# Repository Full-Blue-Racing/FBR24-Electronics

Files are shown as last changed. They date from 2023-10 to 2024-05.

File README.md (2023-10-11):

# FBR24-Electronics

This repo houses all the code the car needs to run, separated into steering 
wheel, telemetry, and CAN bus files.

# Git Gud

[Git Crash Course](https://rogerdudler.github.io/git-guide/)

[Gitlab SSH setup](https://docs.gitlab.com/ee/ssh/)

Git can be separated into remote and local repository (repo), how it works is 
that you can *clone* a repo to your local machine, *add* files you would like 
git to track, *commit* your changes to your local branch, *pull* changes by 
others from the remote repo, and *push* your own local changes. Locally git can 
be separated into three areas:

```Untracked files -> tracked files -> staging area```

Untracked files are usually not part of the project and will not be added to the
repo. Tracked files are project files, and files in here will have status shown 
(i.e. new file/changed/renamed...). The staging area is files that are ready to 
be *committed*, and tracked files needs to be added by ```git add```.

These are the only commands I would recommend using on the command line/IDE, 
for more complex commands (such as creating pull requests for merging branches) 
use the web interface. 

![Image of Git Workflow](https://hackernoon.com/hn-images/1*mQdKYVN0nl-NvTw6MOSkWA.png)

# Best Practices

### No spaces in file names or folder names please

**No direct pushing/committing on the master branch**

1. Use branches

Each of the following tasks are on a separate 
branch, please work on the branch relevant to your task. If multiple people are 
on the same branch please make sub-branches from the main task branch 

*e.g.* 
```
steering-wheel -> steering-wheel-warninglights
               -> steering-wheel-RPM-lights
```

We will merge them into the main steering-wheel branch when you make a merge 
request to the task branch.

2. Micro-commit

Commit every time you've implemented a feature - it allows easy rollback to 
previous version without too much code loss if things go wrong (and they *WILL* 
go wrong).

3. Handy commands

```git config --global user.name <display name>``` - sets your name on your commits to the repo

```git clone <path/to/directory>``` - clones a local copy of the repo to your
machine so you can make changes.

```git pull origin <name of branch>``` - pulls any changes others have 
published on the remote branch of the said name since your last update/ initial 
clone

```git add <file to be added>``` - adds file to the staging area to be included 
in the next commit.

```git commit -m "Commit message here"``` - commits file to the local branch 
with the commit message - please make the commit message meaningful so it is 
easier to backtrack (**Not** ```Add new file```) 

```git push origin <name of branch>``` - push your local commits to the remote 
repo on the named branch. Note that on the first push git may require you to 
set the upstream branch with ```git branch --set-upstream-to <name of head branch>```

```git remote update origin --prune``` - updates branches and removes merged branches 
on your local machine.

# Tasks

Each function to be made are described in respective folders' ```README```,
please edit the ```README``` with your name if you are currently working on the 
task, and remove it if not. If someone is already working on one and you want 
to join, contact them and see if you can help before writing your own code. 
Otherwise just write your name down and contact me (Will) for any 
questions/purchasing.

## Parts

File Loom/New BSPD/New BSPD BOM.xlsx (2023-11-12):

Component Count: | 46
Collated Components:
Item | Qty | Reference(s) | Value | LibPart | Footprint | Datasheet | DNP | Sim.Device | Sim.Pins
1 | 1 | C1 | C | Device:C |  | ~
2 | 1 | D1 | 1N5817 | Diode:1N4001 | Diode_THT:D_DO-41_SOD81_P10.16mm_Horizontal | http://www.vishay.com/docs/88503/1n4001.pdf |  | D | 1=K 2=A
3 | 4 | D2, D3, D4, D5 | LED | Device:LED | LED_THT:LED_D5.0mm | ~
4 | 2 | J1, J2 | 282087-1 | Connector:Conn_01x03_Female | Additional Footprints:3 pin flying lead | https://www.te.com/usa-en/product-282087-1.html
5 | 1 | J3 | 282105-1 | Connector:Conn_01x03_Female | Additional Footprints:3 pin flying lead | https://www.te.com/usa-en/product-282105-1.datasheet.pdf
6 | 1 | J4 | Screw_Terminal_01x02 | Connector:Screw_Terminal_01x02 |  | ~
7 | 4 | JP1, JP2, JP3, JP4 | SolderJumper_3_Open | Jumper:SolderJumper_3_Open | Jumper:SolderJumper-3_P1.3mm_Open_RoundedPad1.0x1.5mm | ~
8 | 1 | K1 | MCCMA51-S-DC12V-C | Additional_Components:Relay | Additional Footprints:MCCMA51-S-DC12V-C | https://www.farnell.com/datasheets/3169904.pdf
9 | 1 | Q1 | IRLZ44Z | Transistor_FET:IRLZ44N | Package_TO_SOT_THT:TO-220-3_Vertical | http://www.irf.com/product-info/datasheets/data/irlz44n.pdf
10 | 2 | R1, R2 | 5Meg | Device:R | Resistor_THT:R_Axial_DIN0207_L6.3mm_D2.5mm_P7.62mm_Horizontal | ~
11 | 1 | R3 | 4.7k | Device:R | Resistor_THT:R_Axial_DIN0207_L6.3mm_D2.5mm_P7.62mm_Horizontal | ~
12 | 4 | R4, R5, R6, R7 | 220R | Device:R | Resistor_THT:R_Axial_DIN0207_L6.3mm_D2.5mm_P7.62mm_Horizontal | ~
13 | 1 | R8 | R | Device:R |  | ~
14 | 4 | RV1, RV2, RV3, RV4 | 10k | Device:R_Potentiometer | Potentiometer_THT:Potentiometer_Bourns_3296Y_Vertical | ~
15 | 1 | RV5 | R_Potentiometer | Device:R_Potentiometer |  | ~
16 | 8 | U1, U2, U3, U4, U5, U6, U7, U8 | 4011 | 4xxx:4011 | Package_DIP:DIP-14_W7.62mm_Socket | http://www.intersil.com/content/dam/Intersil/documents/cd40/cd4011bms-12bms-23bms.pdf
17 | 2 | U9, U10 | LM2901 | Comparator:LM2901 |  | https://www.st.com/resource/en/datasheet/lm2901.pdf
18 | 1 | U11 | 4012 | 4xxx:4012 | Package_DIP:DIP-14_W7.62mm_Socket | http://www.intersil.com/content/dam/Intersil/documents/cd40/cd4011bms-12bms-23bms.pdf
19 | 1 | U12 | 74LS573 | 74xx:74LS573 |  | 74xx/74hc573.pdf
20 | 3 | U13, U14, U15 | 4040 | 4xxx:4040 |  | http://www.intersil.com/content/dam/Intersil/documents/cd40/cd4020bms-24bms-40bms.pdf
21 | 1 | U16 | L7805 | Regulator_Linear:L7805 |  | http://www.st.com/content/ccc/resource/technical/document/datasheet/41/4f/b3/b0/12/d4/47/88/CD00000444.pdf/files/CD00000444.pdf/jcr:content/translations/en.CD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
22 | 1 | X1 | ASZKDV-32.768KHz | BSPD Symbols:ASZKDV-xxxMHz | Oscillator:Oscillator_SMD_Abracon_ASE-4Pin_3.2x2.5mm | http://www.abracon.com/Oscillators/ASV.pdf

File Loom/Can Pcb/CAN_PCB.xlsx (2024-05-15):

# | Reference | Qty | Value | Footprint | DNP
1 | C1, C2 | 2 | 27pF | Capacitor_THT:C_Disc_D4.7mm_W2.5mm_P5.00mm
2 | D1 | 1 | PWR LED | LED_THT:LED_D3.0mm
3 | J2 | 1 | Conn_01x05_Pin | Connector_PinHeader_2.54mm:PinHeader_1x05_P2.54mm_Vertical
4 | J3 | 1 | Screw_Terminal_01x02 | TerminalBlock:TerminalBlock_bornier-2_P5.08mm
5 | J4 | 1 | Conn_01x02 | Footprints:ATF13-2P-BM03
6 | J5, J12, J15, J16 | 4 | Conn_01x03 | BSPD_footprints:ATF13-3P-BM03
7 | JP1, JP4, JP5, JP8 | 4 | SolderJumper_3_Open | Jumper:SolderJumper-3_P1.3mm_Open_Pad1.0x1.5mm | No Fit
8 | R1 | 1 | 20K | Resistor_THT:R_Axial_DIN0207_L6.3mm_D2.5mm_P7.62mm_Horizontal
9 | R2 | 1 | 220R | Resistor_THT:R_Axial_DIN0207_L6.3mm_D2.5mm_P7.62mm_Horizontal
10 | R3, R6, R7, R10 | 4 | 5Meg | Resistor_THT:R_Axial_DIN0207_L6.3mm_D2.5mm_P7.62mm_Horizontal
11 | U1 | 1 | MCP25050-I/P | Package_DIP:DIP-14_W7.62mm_Socket | Sockets and chip
12 | U2 | 1 | MCP2551-I-P | Package_DIP:DIP-8_W7.62mm_Socket | Sockets and chip
13 | U4 | 1 | TL780-05KCS | Package_TO_SOT_THT:TO-220-3_Horizontal_TabDown
14 | Y1 | 1 | Crystal | Footprints:9B-16.000MAAJ-B

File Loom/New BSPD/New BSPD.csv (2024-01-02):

Id | Designator | Footprint | Quantity | Designation | Supplier and ref
1 | D7,D4,D2,D8,D6,D3,D5 | LED_D5.0mm | 7 | LED
2 | R10,R11,R7,R9,R6,R5,R4 | R_Axial_DIN0207_L6.3mm_D2.5mm_P7.62mm_Horizontal | 7 | 220R
3 | JP1,JP2,JP4,JP3 | SolderJumper-3_P1.3mm_Open_RoundedPad1.0x1.5mm | 4 | SolderJumper_3_Open
4 | U12 | DIP-20_W7.62mm_Socket | 1 | 74LS573
5 | U3,U5,U2,U6,U8,U1,U7,U4 | DIP-14_W7.62mm_Socket | 8 | 4011
6 | RV2,RV3,RV1,RV4 | Potentiometer_Bourns_3296Y_Vertical | 4 | 10k
7 | C1 | C_Disc_D5.0mm_W2.5mm_P5.00mm | 1 | 100n
8 | U11 | DIP-14_W7.62mm_Socket | 1 | 4012
9 | U14,U13,U15 | DIP-16_W7.62mm_Socket | 3 | 4040
10 | K1 | MCCMA51-S-DC12V-C | 1 | MCCMA51-S-DC12V-C
11 | R3 | R_Axial_DIN0207_L6.3mm_D2.5mm_P7.62mm_Horizontal | 1 | 4.7k
12 | R8 | R_Axial_DIN0207_L6.3mm_D2.5mm_P7.62mm_Horizontal | 1 | 1M
13 | TP4,TP3,TP2,TP1 | TestPoint_THTPad_D3.0mm_Drill1.5mm | 4 | TestPoint
14 | J3,J2,J1 | ATF13-3P-BM03 | 3 | Conn_01x03
15 | Q1 | TO-220-3_Horizontal_TabDown | 1 | IRLZ44Z
16 | U9,U10 | DIP-14_W7.62mm_Socket | 2 | LM2901
17 | C2 | C_0603_1608Metric_Pad1.08x0.95mm_HandSolder | 1 | 10u
18 | U16 | TO-220-3_Horizontal_TabDown | 1 | L7805
19 | X1 | Oscillator_SMD_Abracon_ASE-4Pin_3.2x2.5mm | 1 | ASZKDV-32.768KHz
20 | D1 | D_DO-41_SOD81_P10.16mm_Horizontal | 1 | 1N5817
21 | R1,R2 | R_Axial_DIN0207_L6.3mm_D2.5mm_P7.62mm_Horizontal | 2 | 5Meg
22 | J4 | TerminalBlock_bornier-2_P5.08mm | 1 | Screw_Terminal_01x02
23 | RV5 | Potentiometer_Bourns_3296Y_Vertical | 1 | R_Potentiometer

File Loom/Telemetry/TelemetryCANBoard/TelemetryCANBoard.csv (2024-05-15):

Source: | /home/charlotte/Documents/FBR/FBR24-Electronics/Loom/Telemetry/TelemetryCANBoard/TelemetryCANBoard.kicad_sch
Date: | Sun 12 Nov 2023 15:14:25 GMT
Tool: | Eeschema 7.0.8
Generator: | /usr/share/kicad/plugins/bom_csv_grouped_by_value.py
Component Count: | 11
Collated Components:
Item | Qty | Reference(s) | Value | LibPart | Footprint | Datasheet | DNP
1 | 2 | C1, C2 | 27p | Device:C_Small |  | ~
2 | 2 | J1, J2 | Conn_01x06 | Connector_Generic:Conn_01x06 |  | ~
3 | 1 | J3 | Conn_01x02 | Connector_Generic:Conn_01x02 |  | ~
4 | 1 | R1 | 20k | Device:R |  | ~
5 | 1 | R2 | 10k | Device:R |  | ~
6 | 1 | R3 | 120 | Device:R |  | ~
7 | 1 | U1 | MCP2551-I-P | Interface_CAN_LIN:MCP2551-I-P | Package_DIP:DIP-8_W7.62mm | http://ww1.microchip.com/downloads/en/devicedoc/21667d.pdf
8 | 1 | U2 | MCP2515-xSO | Interface_CAN_LIN:MCP2515-xSO | Package_SO:SOIC-18W_7.5x11.6mm_P1.27mm | http://ww1.microchip.com/downloads/en/DeviceDoc/21801e.pdf
9 | 1 | Y1 | 16M | Device:Crystal |  | ~

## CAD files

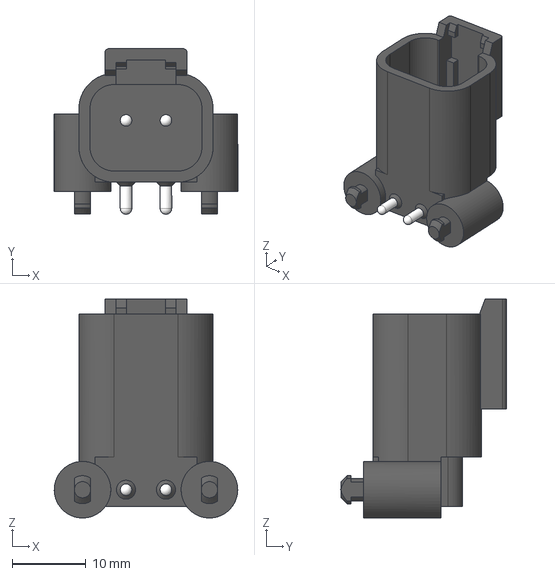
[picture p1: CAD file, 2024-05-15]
Loom/Can Pcb/Footprints/AMPHENOLSINE_ATF132PBM03/ATF13-2P-BM03.stp
24.8 x 22.4 x 29.6 mm

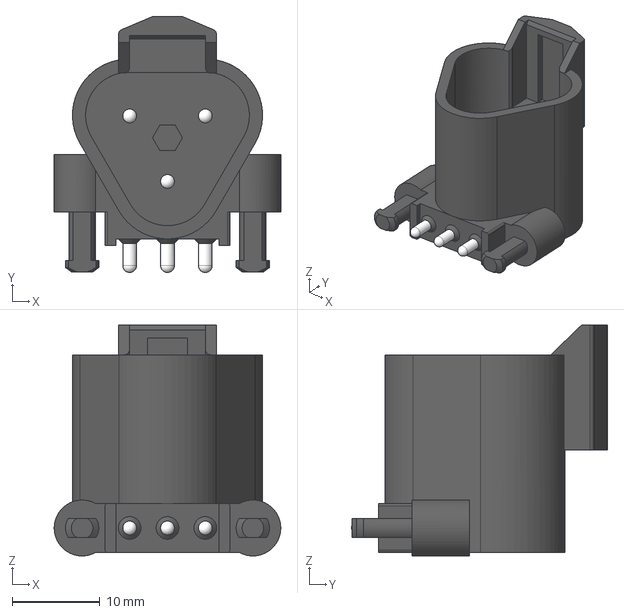
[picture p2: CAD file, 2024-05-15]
Loom/Can Pcb/Footprints/AMPHENOLSINE_ATF133PBM03 2/ATF13-3P-BM03.stp
25.8 x 29.1 x 26.3 mm

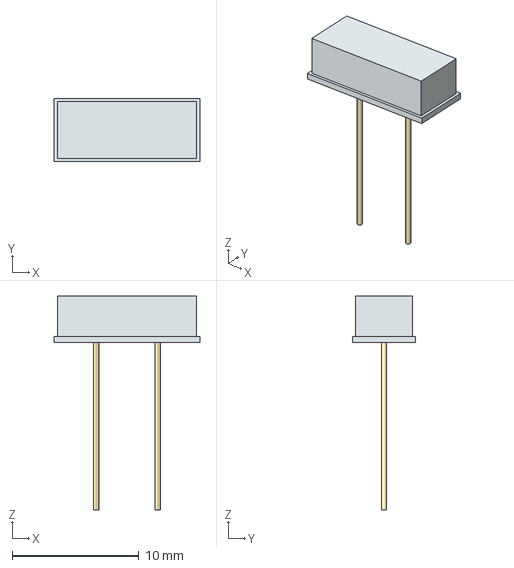
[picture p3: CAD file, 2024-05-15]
Loom/Can Pcb/Footprints/LIB_9B-16.000MAAJ-B/9B-16.000MAAJ-B/3D/9B-16.000MAAJ-B.stp
11.5 x 5.00 x 16.9 mm
solidBody
solidLead

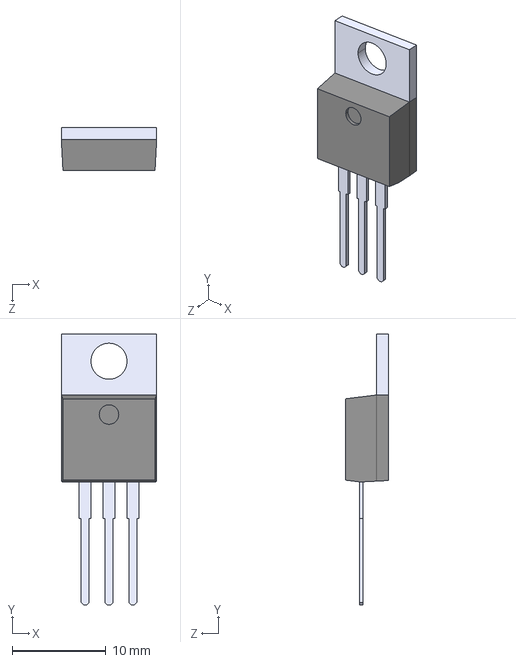
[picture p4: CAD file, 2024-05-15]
Loom/Can Pcb/Footprints/TO254P1036X470X1965-3.step
10.2 x 28.9 x 4.55 mm

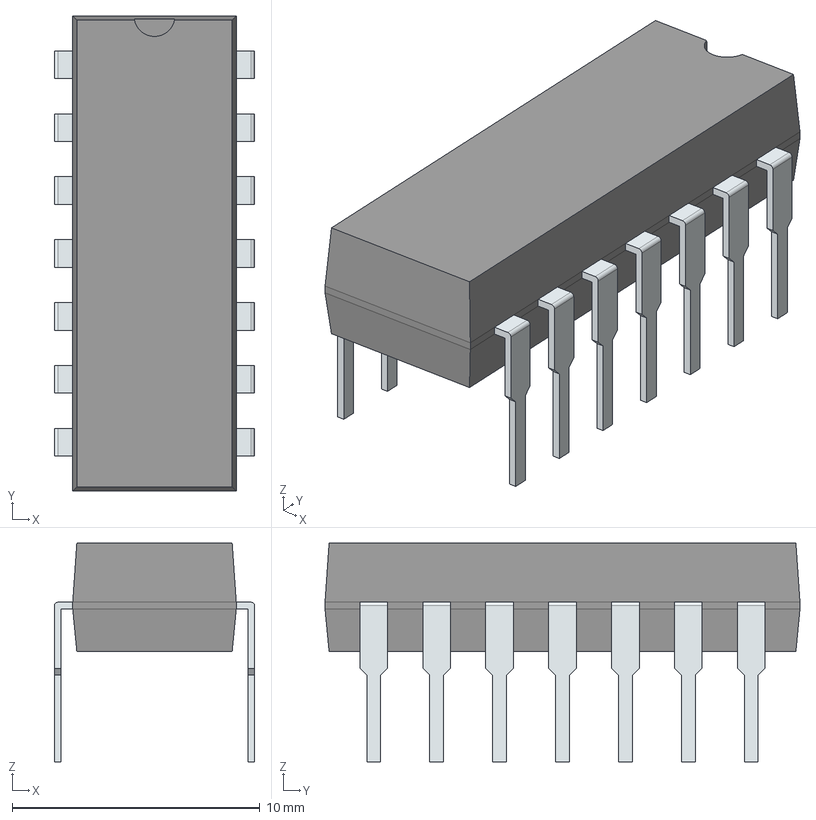
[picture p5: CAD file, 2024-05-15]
Loom/Can Pcb/Footprints/mcp6004-e_p.stp
8.09 x 19.2 x 8.83 mm
PinsArrayLR

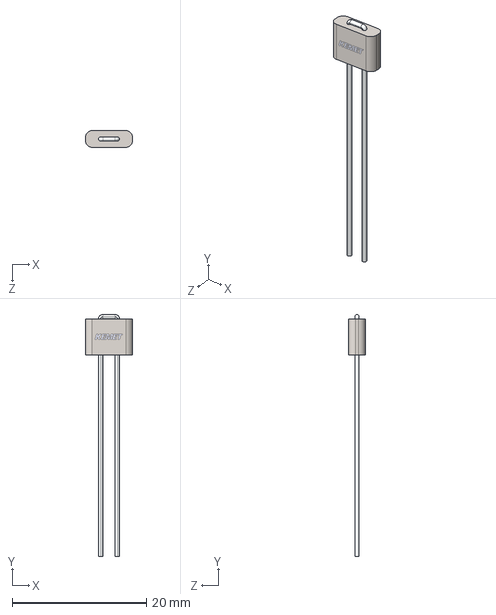
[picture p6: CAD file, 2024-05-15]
Loom/Can Pcb/Footprints/B-06-R-25.step
7.00 x 36.0 x 2.50 mm

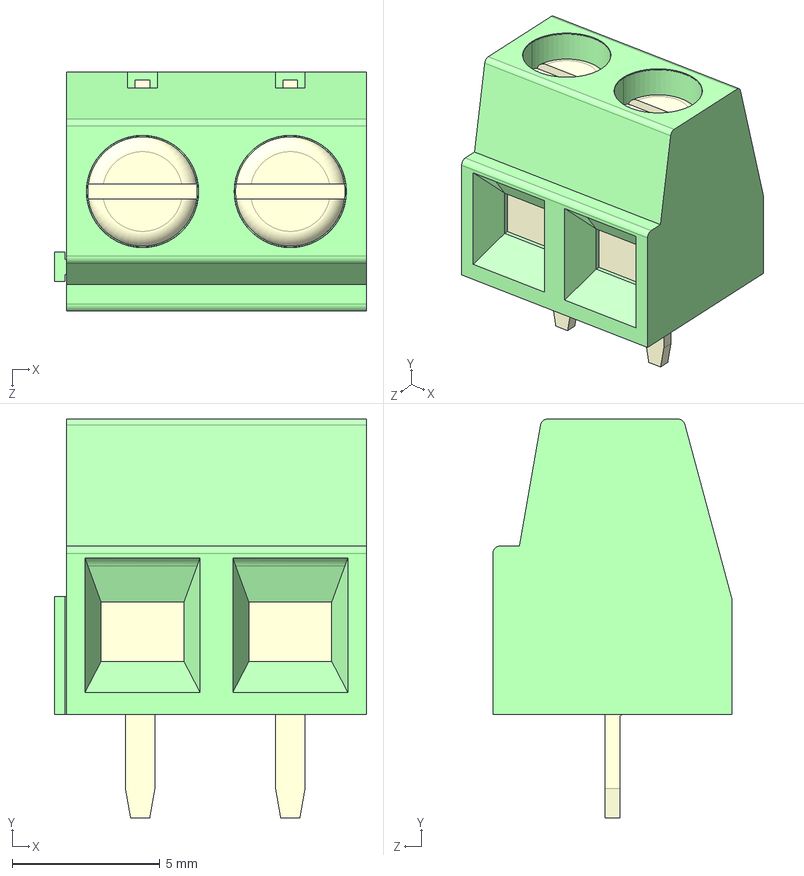
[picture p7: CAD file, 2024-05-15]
Loom/Can Pcb/Footprints/LIB_1729128/1729128/3D/1729128.stp
10.6 x 13.5 x 8.10 mm

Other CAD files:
Loom/Can Pcb/Footprints/AMPHENOLSINE_ATF133PBM03/ATF13-3P-BM03.stl
Loom/Can Pcb/Footprints/LIB_1729128/1729128/Allegro/1729128.psm
Loom/Can Pcb/Footprints/LIB_1729128/1729128/DEHDL/1729128/chips/chips.prt
Loom/Can Pcb/Footprints/LIB_9B-16.000MAAJ-B/9B-16.000MAAJ-B/Allegro/9b16000maajb.psm
Loom/Can Pcb/Footprints/LIB_9B-16.000MAAJ-B/9B-16.000MAAJ-B/DEHDL/9b_16.000maaj_b/chips/chips.prt

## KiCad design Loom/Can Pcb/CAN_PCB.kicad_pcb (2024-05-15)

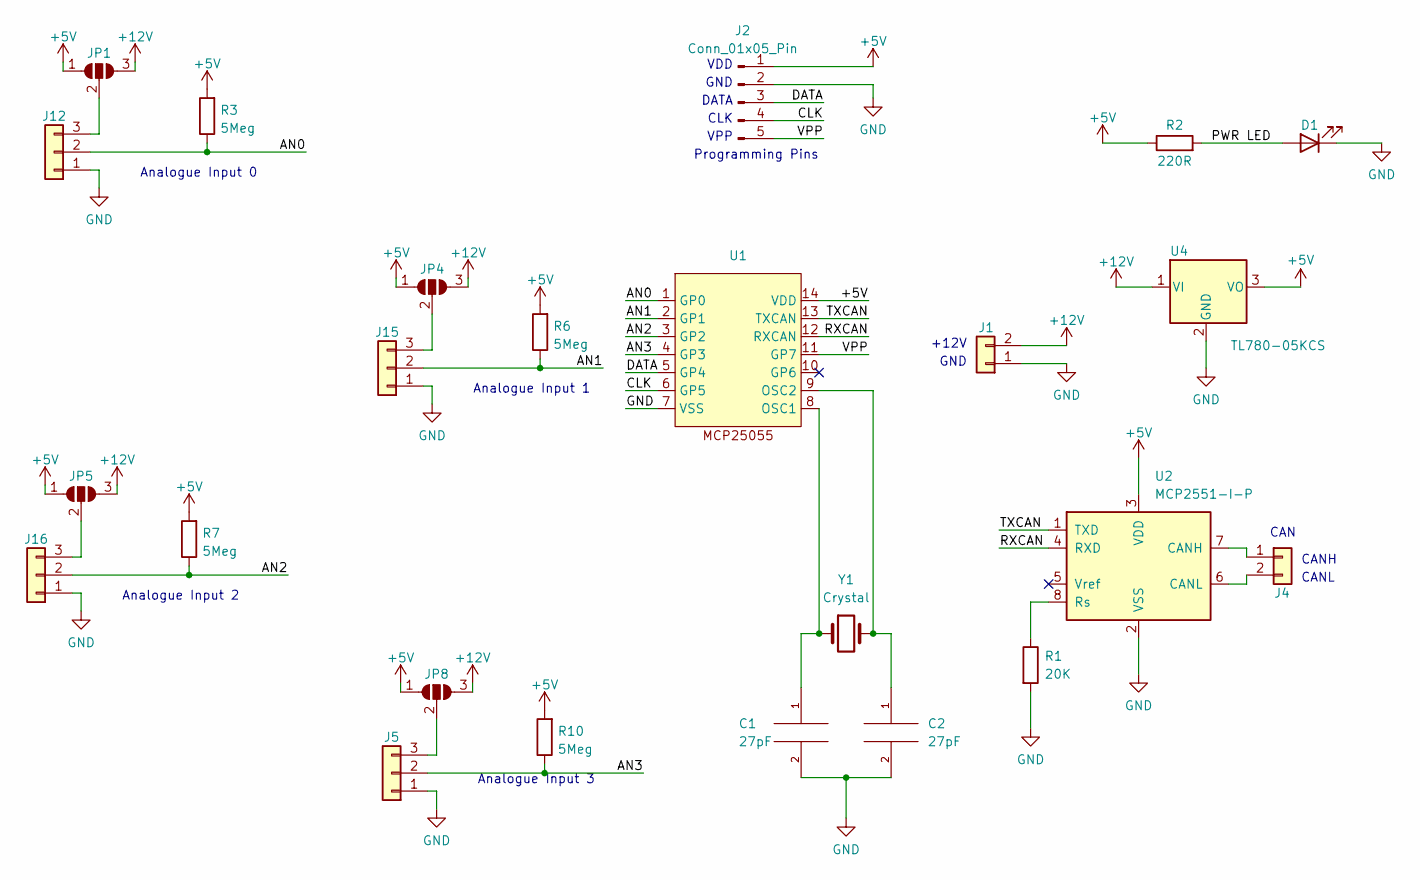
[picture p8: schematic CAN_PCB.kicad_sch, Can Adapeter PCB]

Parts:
C1, C2: 27pF; C_Disc_D4.7mm_W2.5mm_P5.00mm
D1: PWR LED; LED_D3.0mm
J1, J4: Conn_01x02; ATF13-2P-BM03
J2: Conn_01x05_Pin; PinHeader_1x05_P2.54mm_Vertical
J5, J12, J15, J16: Conn_01x03; ATF13-3P-BM03
JP1, JP4, JP5, JP8: SolderJumper_3_Open; SolderJumper-3_P1.3mm_Open_Pad1.0x1.5mm
R1: 20K; R_Axial_DIN0207_L6.3mm_D2.5mm_P7.62mm_Horizontal
R2: 220R; R_Axial_DIN0207_L6.3mm_D2.5mm_P7.62mm_Horizontal
R3, R6, R7, R10: 5Meg; R_Axial_DIN0207_L6.3mm_D2.5mm_P7.62mm_Horizontal
U1: DIP-14_W7.62mm_Socket
U2: MCP2551-I-P; DIP-8_W7.62mm_Socket
U4: TL780-05KCS; TO-220-3_Horizontal_TabDown
Y1: Crystal; 9B-16.000MAAJ-B

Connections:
+5V: J2.1, JP1.1 (A), JP4.1 (A), JP5.1 (A), JP8.1 (A), R2.1, R3.2, R6.2, R7.2, R10.2, U1.14 (VDD), U2.3 (VDD), U4.3 (VO)
+12V: J1.2, JP1.3 (B), JP4.3 (B), JP5.3 (B), JP8.3 (B), U4.1 (VI)
/AN0: J12.2, R3.1, U1.1 (GP0)
/AN1: J15.2, R6.1, U1.2 (GP1)
/AN2: J16.2, R7.1, U1.3 (GP2)
/AN3: J5.2, R10.1, U1.4 (GP3)
/CLK: J2.4, U1.6 (GP5)
/DATA: J2.3, U1.5 (GP4)
/PWR LED: D1.2 (A), R2.2
/RXCAN: U1.12 (RXCAN), U2.4 (RXD)
/TXCAN: U1.13 (TXCAN), U2.1 (TXD)
/VPP: J2.5, U1.11 (GP7)
GND: C1.2, C2.2, D1.1 (K), J1.1, J2.2, J5.1, J12.1, J15.1, J16.1, R1.2, U1.7 (VSS), U2.2 (VSS), U4.2 (GND)
unnamed: J4.1, U2.7 (CANH)
unnamed: J4.2, U2.6 (CANL)
unnamed: J5.3, JP8.2 (C)
unnamed: J12.3, JP1.2 (C)
unnamed: J15.3, JP4.2 (C)
unnamed: J16.3, JP5.2 (C)
unnamed: C1.1, U1.8 (OSC1), Y1.1
unnamed: C2.1, U1.9 (OSC2), Y1.2
unnamed: R1.1, U2.8 (Rs)

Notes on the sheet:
CAN
DATA
+12V
Analogue Input 2
VDD
Programming Pins
CANL
Analogue Input 3
Analogue Input 0
VPP
GND
CANH
CLK
Analogue Input 1

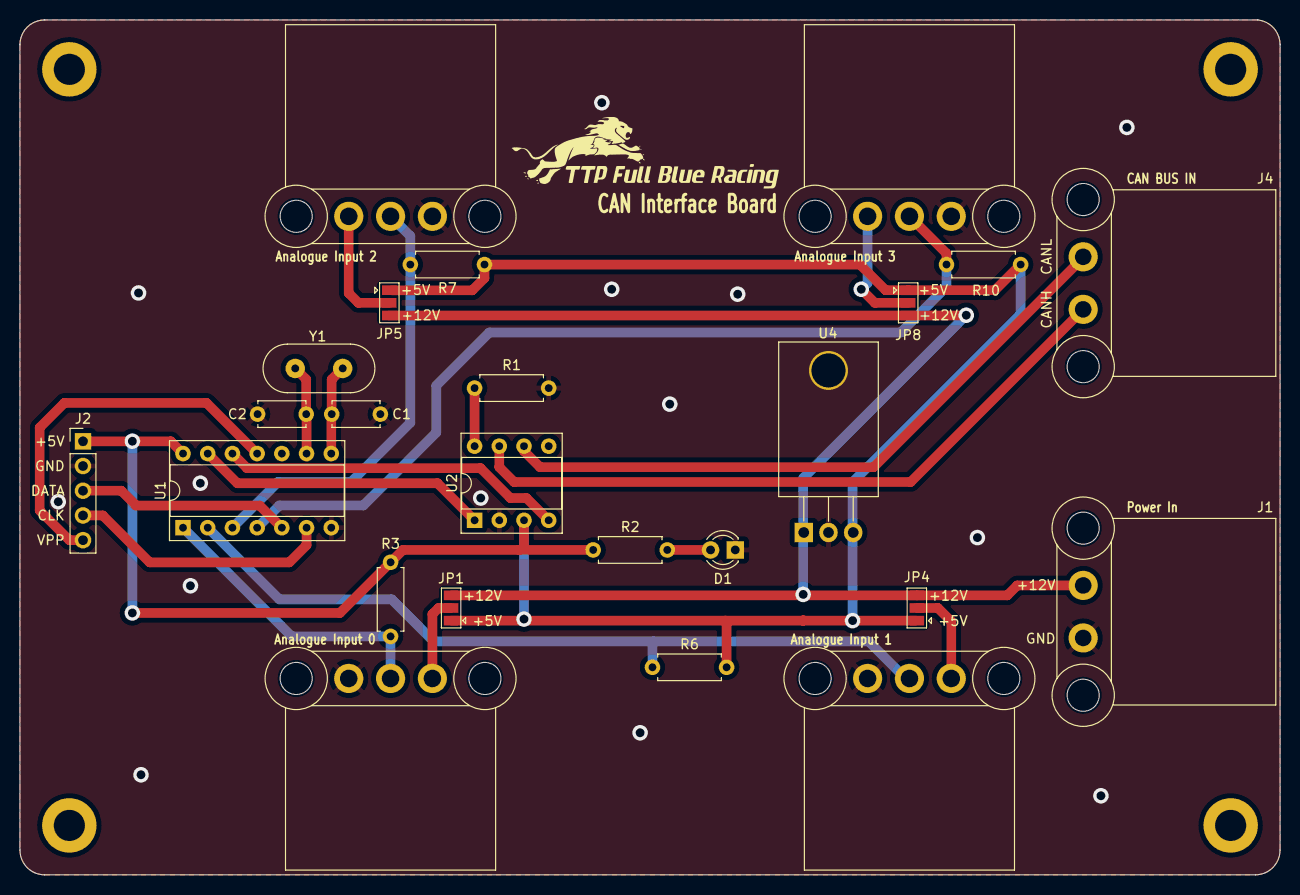
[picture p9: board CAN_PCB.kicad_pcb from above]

Board: 2 copper layers, 129.5 x 87.9 mm, 24 parts (0 on the bottom side), 22 nets.

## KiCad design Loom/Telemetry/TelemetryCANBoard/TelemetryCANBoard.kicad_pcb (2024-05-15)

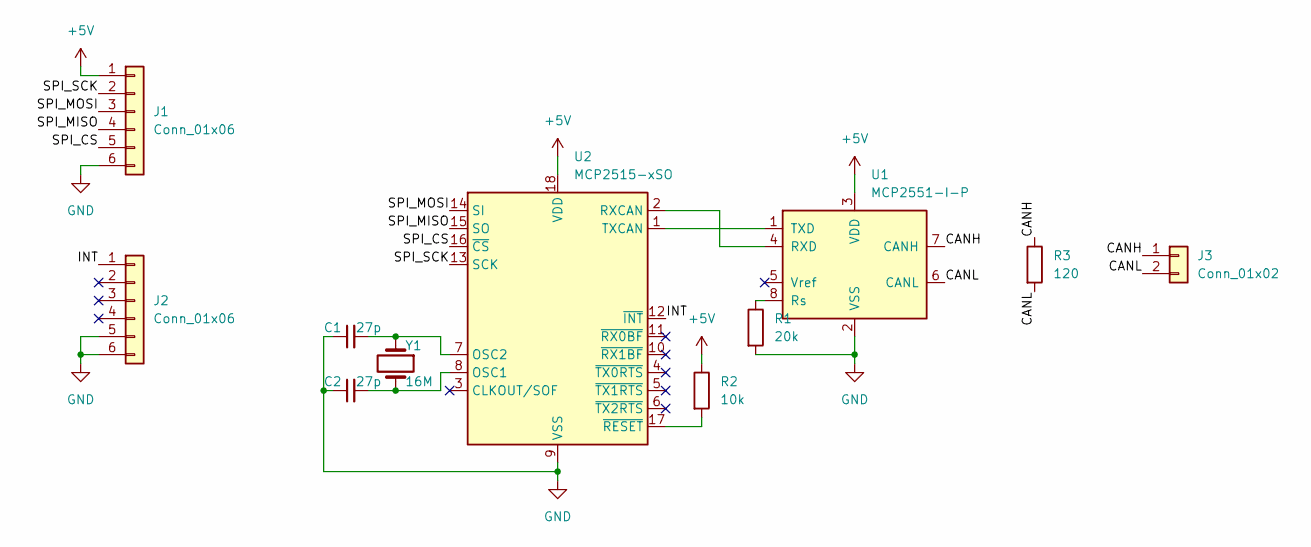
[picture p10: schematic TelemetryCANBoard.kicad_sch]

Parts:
C1, C2: 27p; C_Disc_D5.1mm_W3.2mm_P5.00mm
J1, J2: Conn_01x06; JST_XA_B06B-XASK-1_1x06_P2.50mm_Vertical
J3: Conn_01x02; ATF13-2P-BM03
R1: 20k; R_Axial_DIN0207_L6.3mm_D2.5mm_P7.62mm_Horizontal
R2: 10k; R_Axial_DIN0207_L6.3mm_D2.5mm_P7.62mm_Horizontal
R3: 120; R_Axial_DIN0207_L6.3mm_D2.5mm_P7.62mm_Horizontal
U1: MCP2551-I-P; DIP-8_W7.62mm
U2: MCP2515-xSO; DIP-18_W7.62mm
Y1: 16M; Crystal_HC49-U_Vertical

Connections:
+5V: J1.1, R2.1, U1.3 (VDD), U2.18 (VDD)
/CANH: J3.1, R3.1, U1.7 (CANH)
/CANL: J3.2, R3.2, U1.6 (CANL)
/INT: J2.1, U2.12 (~INT)
/SPI_CS: J1.5, U2.16 (~CS)
/SPI_MISO: J1.4, U2.15 (SO)
/SPI_MOSI: J1.3, U2.14 (SI)
/SPI_SCK: J1.2, U2.13 (SCK)
GND: C1.1, C2.1, J1.6, J2.5, J2.6, R1.2, U1.2 (VSS), U2.9 (VSS)
unnamed: U1.4 (RXD), U2.2 (RXCAN)
unnamed: R1.1, U1.8 (Rs)
unnamed: U1.1 (TXD), U2.1 (TXCAN)
unnamed: C2.2, U2.8 (OSC1), Y1.2
unnamed: C1.2, U2.7 (OSC2), Y1.1
unnamed: R2.2, U2.17 (~RESET)

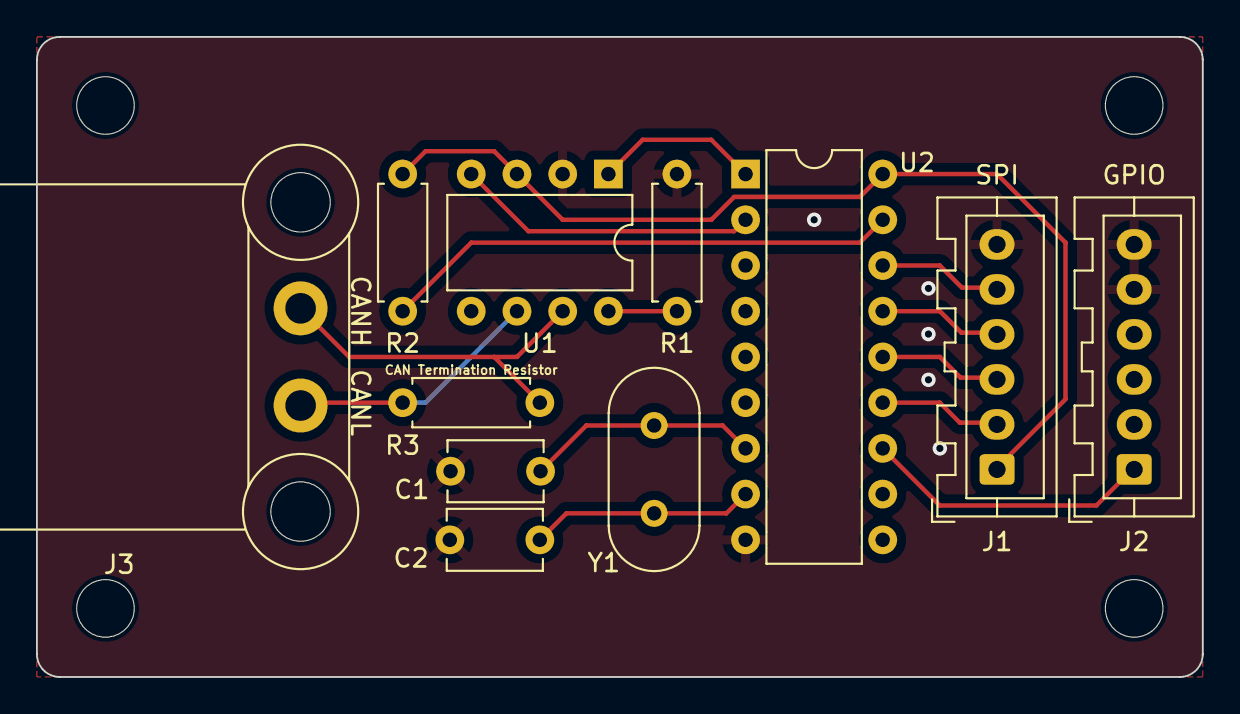
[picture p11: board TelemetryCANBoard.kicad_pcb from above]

Board: 2 copper layers, 64.8 x 35.6 mm, 15 parts (0 on the bottom side), 15 nets.

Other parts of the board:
MNT1, MNT3, MNT4: MountingHole_3.2mm_M3
MNT2: MountingHole_3.2mm_M; MountingHole_3.2mm_M3

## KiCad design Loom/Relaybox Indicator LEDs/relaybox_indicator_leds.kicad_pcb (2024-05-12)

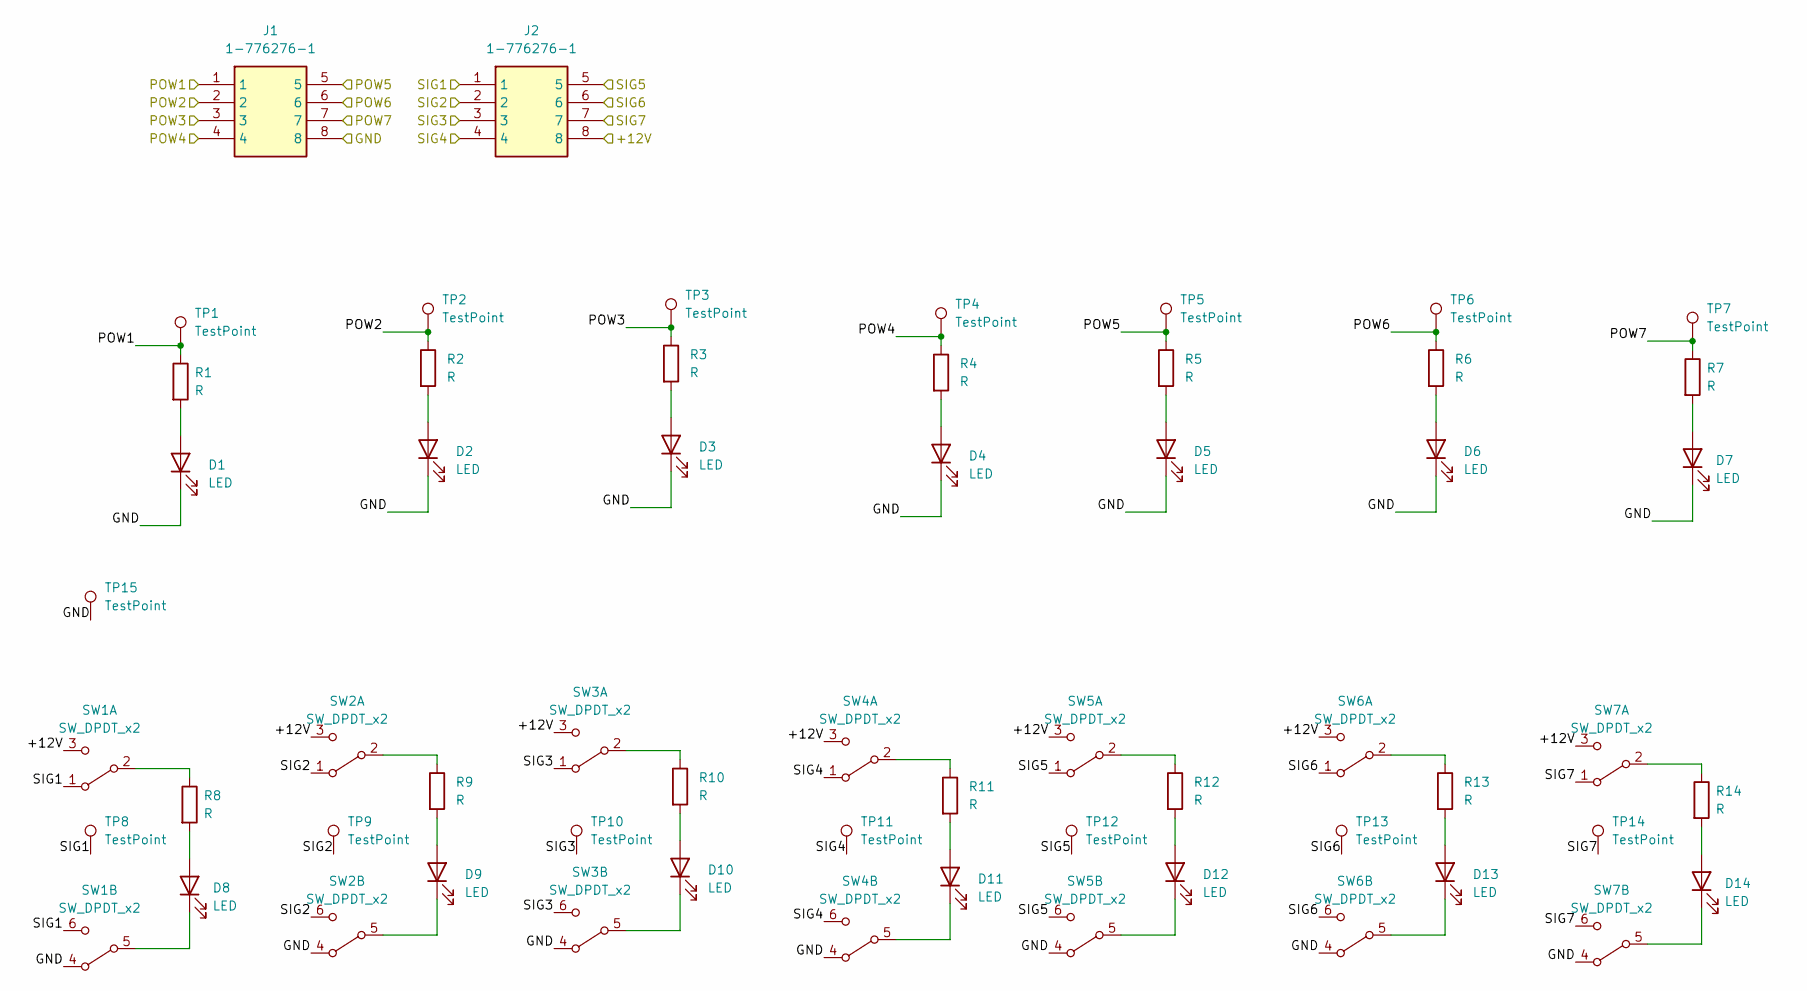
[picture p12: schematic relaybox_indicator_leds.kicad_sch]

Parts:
D1, D2, D3, D4, D5, D6, D7, D8, D9, D10, D11, D12, D13, D14: LED; LED_D5.0mm
J1, J2: 1-776276-1; 17762761; Mouser Part Number 571-1-776276-1
R1, R2, R3, R4, R5, R6, R7, R8, R9, R10, R11, R12, R13, R14: R; R_Axial_DIN0207_L6.3mm_D2.5mm_P10.16mm_Horizontal
SW1, SW2, SW3, SW4, SW5, SW6, SW7: SW_DPDT_x2; MP004696
TP1, TP2, TP3, TP4, TP5, TP6, TP7, TP8, TP9, TP10, TP11, TP12, TP13, TP14, TP15: TestPoint; TestPoint_THTPad_D3.0mm_Drill1.5mm

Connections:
/+12V: J2.8, SW1.3 (C), SW2.3 (C), SW3.3 (C), SW4.3 (C), SW5.3 (C), SW6.3 (C), SW7.3 (C)
/GND: D1.1 (K), D2.1 (K), D3.1 (K), D4.1 (K), D5.1 (K), D6.1 (K), D7.1 (K), J1.8, SW1.4 (A), SW2.4 (A), SW3.4 (A), SW4.4 (A), SW5.4 (A), SW6.4 (A), SW7.4 (A), TP15.1
/POW1: J1.1, R1.1, TP1.1
/POW2: J1.2, R2.1, TP2.1
/POW3: J1.3, R3.1, TP3.1
/POW4: J1.4, R4.1, TP4.1
/POW5: J1.5, R5.1, TP5.1
/POW6: J1.6, R6.1, TP6.1
/POW7: J1.7, R7.1, TP7.1
/SIG1: J2.1, SW1.1 (A), SW1.6 (C), TP8.1
/SIG2: J2.2, SW2.1 (A), SW2.6 (C), TP9.1
/SIG3: J2.3, SW3.1 (A), SW3.6 (C), TP10.1
/SIG4: J2.4, SW4.1 (A), SW4.6 (C), TP11.1
/SIG5: J2.5, SW5.1 (A), SW5.6 (C), TP12.1
/SIG6: J2.6, SW6.1 (A), SW6.6 (C), TP13.1
/SIG7: J2.7, SW7.1 (A), SW7.6 (C), TP14.1
unnamed: D1.2 (A), R1.2
unnamed: D2.2 (A), R2.2
unnamed: D3.2 (A), R3.2
unnamed: D4.2 (A), R4.2
unnamed: D5.2 (A), R5.2
unnamed: D6.2 (A), R6.2
unnamed: D7.2 (A), R7.2
unnamed: D8.2 (A), R8.2
unnamed: D8.1 (K), SW1.5 (B)
unnamed: D9.2 (A), R9.2
unnamed: D9.1 (K), SW2.5 (B)
unnamed: D10.2 (A), R10.2
unnamed: D10.1 (K), SW3.5 (B)
unnamed: D11.2 (A), R11.2
unnamed: D11.1 (K), SW4.5 (B)
unnamed: D12.2 (A), R12.2
unnamed: D12.1 (K), SW5.5 (B)
unnamed: D13.2 (A), R13.2
unnamed: D13.1 (K), SW6.5 (B)
unnamed: D14.2 (A), R14.2
unnamed: D14.1 (K), SW7.5 (B)
unnamed: R8.1, SW1.2 (B)
unnamed: R9.1, SW2.2 (B)
unnamed: R10.1, SW3.2 (B)
unnamed: R11.1, SW4.2 (B)
unnamed: R12.1, SW5.2 (B)
unnamed: R13.1, SW6.2 (B)
unnamed: R14.1, SW7.2 (B)

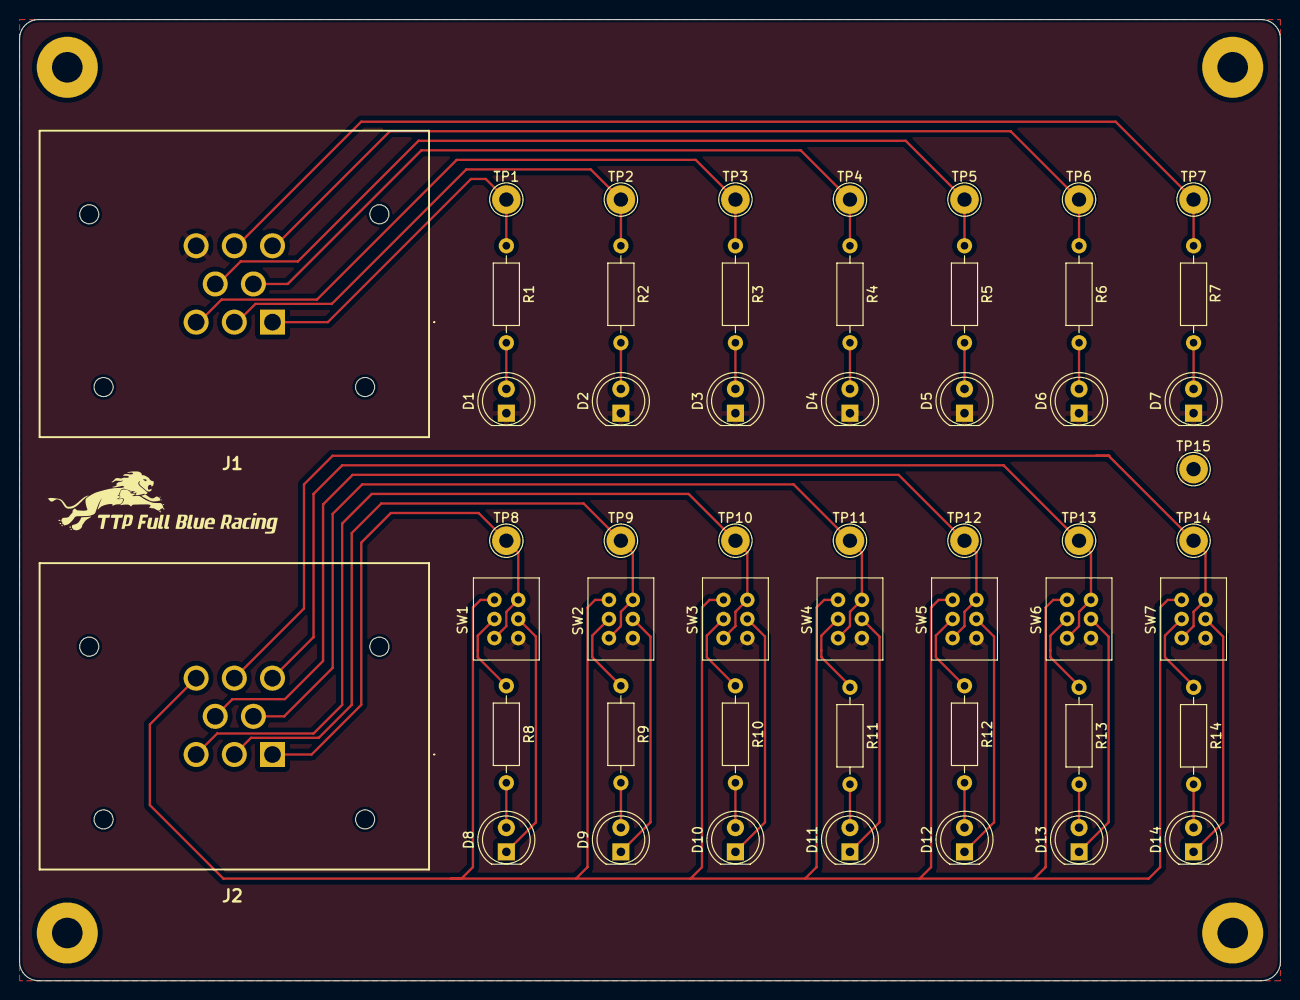
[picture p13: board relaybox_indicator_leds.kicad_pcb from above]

Board: 2 copper layers, 132.1 x 100.7 mm, 52 parts (0 on the bottom side), 44 nets.

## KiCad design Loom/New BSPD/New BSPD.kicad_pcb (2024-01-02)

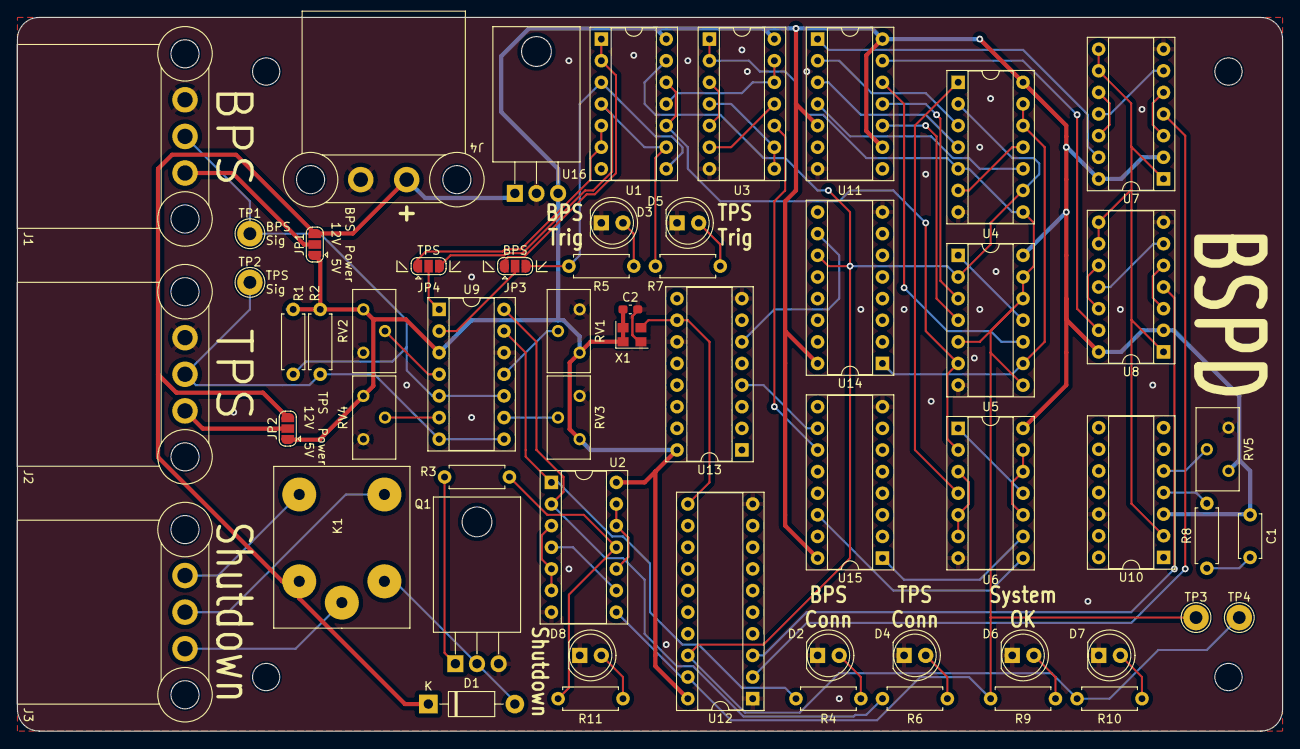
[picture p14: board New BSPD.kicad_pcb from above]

Board: 2 copper layers, 148.6 x 83.8 mm, 61 parts (0 on the bottom side), 75 nets.

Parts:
C1: 100n; C_Disc_D5.0mm_W2.5mm_P5.00mm
C2: 10u; C_0603_1608Metric_Pad1.08x0.95mm_HandSolder
D1: 1N5817; D_DO-41_SOD81_P10.16mm_Horizontal
D2, D3, D4, D5, D6, D7, D8: LED; LED_D5.0mm
J1, J2, J3: Conn_01x03; ATF13-3P-BM03
J4: Screw_Terminal_01x02; ATF13-2P-BM03
JP1, JP2, JP3, JP4: SolderJumper_3_Open; SolderJumper-3_P1.3mm_Open_RoundedPad1.0x1.5mm
K1: MCCMA51-S-DC12V-C
MNT1, MNT2, MNT3, MNT4: MountingHole_3.2mm_M3
Q1: IRLZ44Z; TO-220-3_Horizontal_TabDown
R1, R2: 5Meg; R_Axial_DIN0207_L6.3mm_D2.5mm_P7.62mm_Horizontal
R3: 4.7k; R_Axial_DIN0207_L6.3mm_D2.5mm_P7.62mm_Horizontal
R4, R5, R6, R7, R9, R10, R11: 220R; R_Axial_DIN0207_L6.3mm_D2.5mm_P7.62mm_Horizontal
R8: 1M; R_Axial_DIN0207_L6.3mm_D2.5mm_P7.62mm_Horizontal
RV1, RV2, RV3, RV4: 10k; Potentiometer_Bourns_3296Y_Vertical
RV5: R_Potentiometer; Potentiometer_Bourns_3296Y_Vertical
TP1, TP2, TP3, TP4: TestPoint; TestPoint_THTPad_D3.0mm_Drill1.5mm
U1, U2, U3, U4, U5, U6, U7, U8: 4011; DIP-14_W7.62mm_Socket
U9, U10: LM2901; DIP-14_W7.62mm_Socket
U11: 4012; DIP-14_W7.62mm_Socket
U12: 74LS573; DIP-20_W7.62mm_Socket
U13, U14, U15: 4040; DIP-16_W7.62mm_Socket
U16: L7805; TO-220-3_Horizontal_TabDown
X1: ASZKDV-32.768KHz; Oscillator_SMD_Abracon_ASE-4Pin_3.2x2.5mm

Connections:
+5V: C1.1, C2.1, JP1.1 (A), JP2.1 (A), R1.2, R2.2, RV1.1, RV2.1, RV3.1, RV4.1, RV5.1, U1.14 (VDD), U2.14 (VDD), U3.14 (VDD), U4.14 (VDD), U5.14 (VDD), U6.14 (VDD), U7.2, U7.14 (VDD), U8.2, U8.14 (VDD), U9.3 (V+), U10.3 (V+), U11.5, U11.9, U11.14 (VDD), U12.20 (VCC), U13.16 (VDD), U14.16 (VDD), U15.16 (VDD), U16.3 (OUT), X1.1 (EN), X1.4 (Vdd)
+12V: D1.1 (K), J4.1, JP1.3 (B), JP2.3 (B), K1.2, U16.1 (IN)
/BPS_Plugged: R4.2, U2.1, U9.13
/BPS_Power: J1.3, JP1.2 (C)
/BPS_Sig: J1.2, R1.1, TP1.1, U9.5 (+), U9.10 (-)
/BPS_Trig: JP3.3 (B), R5.2, U1.3, U1.8
/CLK: U12.11 (Load), U13.10 (CLK), X1.3 (OUT)
/RST: U7.1, U7.8, U7.9, U8.1, U8.8, U8.9, U10.2
/SD_Sig: R3.1, R11.2, U2.11
/SM_Ok: R9.2, TP3.1, U2.8, U3.1, U3.2, U4.5, U4.8, U5.5, U5.8, U5.12, U5.13, U12.19 (Q0)
/ShutdownC: J3.3, K1.4
/ShutdownNC: J3.2, K1.3
/ShutdownNO: J3.1, K1.5
/State Machine/5T: U4.12, U4.13, U5.9, U14.1 (Q11)
/State Machine/10T: U6.1, U6.11
/State Machine/State_B: R10.2, TP4.1, U1.13, U4.2, U4.9, U5.2, U12.18 (Q1), U14.11 (Reset)
/State Machine/Timers/256CLK: U13.4 (Q6), U15.10 (CLK)
/State Machine/Timers/4096CLK: U13.6 (Q2), U14.10 (CLK)
/State Machine/Timers/Reset_Counting: U3.10, U15.11 (Reset)
/System_OK: U1.10, U1.12, U5.6, U6.2
/TPS_Plugged: R6.2, U2.2, U9.14
/TPS_Power: J2.3, JP2.2 (C)
/TPS_Sig: J2.2, R2.1, TP2.1, U9.7 (+), U9.8 (-)
/TPS_Trig: JP4.3 (B), R7.2, U1.4, U1.9
GND: C2.2, D2.1 (K), D3.1 (K), D4.1 (K), D5.1 (K), D6.1 (K), D7.1 (K), D8.1 (K), J1.1, J2.1, J4.2, Q1.3 (S), RV1.3, RV2.3, RV3.3, RV4.3, RV5.3, U1.7 (VSS), U2.7 (VSS), U3.7 (VSS), U4.7 (VSS), U5.7 (VSS), U6.7 (VSS), U7.7 (VSS), U8.7 (VSS), U9.12 (V-), U10.12 (V-), U11.7 (VSS), U12.1 (OE), U12.10 (GND), U13.8 (VSS), U13.11 (Reset), U14.8 (VSS), U15.8 (VSS), U16.2 (GND), X1.2 (GND)
unnamed: C1.2, R8.1
unnamed: D1.2 (A), K1.1, Q1.2 (D)
unnamed: D2.2 (A), R4.1
unnamed: D3.2 (A), R5.1
unnamed: D4.2 (A), R6.1
unnamed: D5.2 (A), R7.1
unnamed: D6.2 (A), R9.1
unnamed: D7.2 (A), R10.1
unnamed: D8.2 (A), R11.1
unnamed: JP3.1 (A), U1.1, U1.2
unnamed: JP3.2 (C), U9.2
unnamed: JP4.1 (A), U1.5, U1.6
unnamed: JP4.2 (C), U9.1
unnamed: Q1.1 (G), R3.2
unnamed: U1.11, U3.12, U3.13
unnamed: U2.3, U2.5, U2.6
unnamed: U2.4, U2.9
unnamed: U2.10, U2.12, U2.13
unnamed: U3.3, U3.5
unnamed: U3.4, U3.8, U3.9
unnamed: U3.6, U3.11
unnamed: U4.1, U6.4
unnamed: U4.6, U4.11
unnamed: U5.1, U5.11
unnamed: U6.3, U6.5, U6.6
unnamed: U6.10, U6.12, U6.13
unnamed: U7.3, U7.5
unnamed: U7.10, U7.12
unnamed: U7.6, U7.11
unnamed: U8.3, U8.5
unnamed: U8.10, U8.12
unnamed: U8.6, U8.11
unnamed: RV2.2, U9.4 (-)
unnamed: RV4.2, U9.6 (-)
unnamed: RV1.2, U9.11 (+)
unnamed: RV3.2, U9.9 (+)
unnamed: RV5.2, U10.5 (+)
unnamed: R8.2, U10.4 (-)
unnamed: U7.13, U11.1
unnamed: U4.3, U11.2
unnamed: U4.4, U11.3
unnamed: U4.10, U11.4
unnamed: U5.4, U11.10
unnamed: U5.3, U11.11
unnamed: U5.10, U11.12
unnamed: U8.13, U11.13
unnamed: U7.4, U12.2 (D0)
unnamed: U8.4, U12.3 (D1)
unnamed: U6.8, U15.14 (Q9)
unnamed: U6.9, U15.1 (Q11)

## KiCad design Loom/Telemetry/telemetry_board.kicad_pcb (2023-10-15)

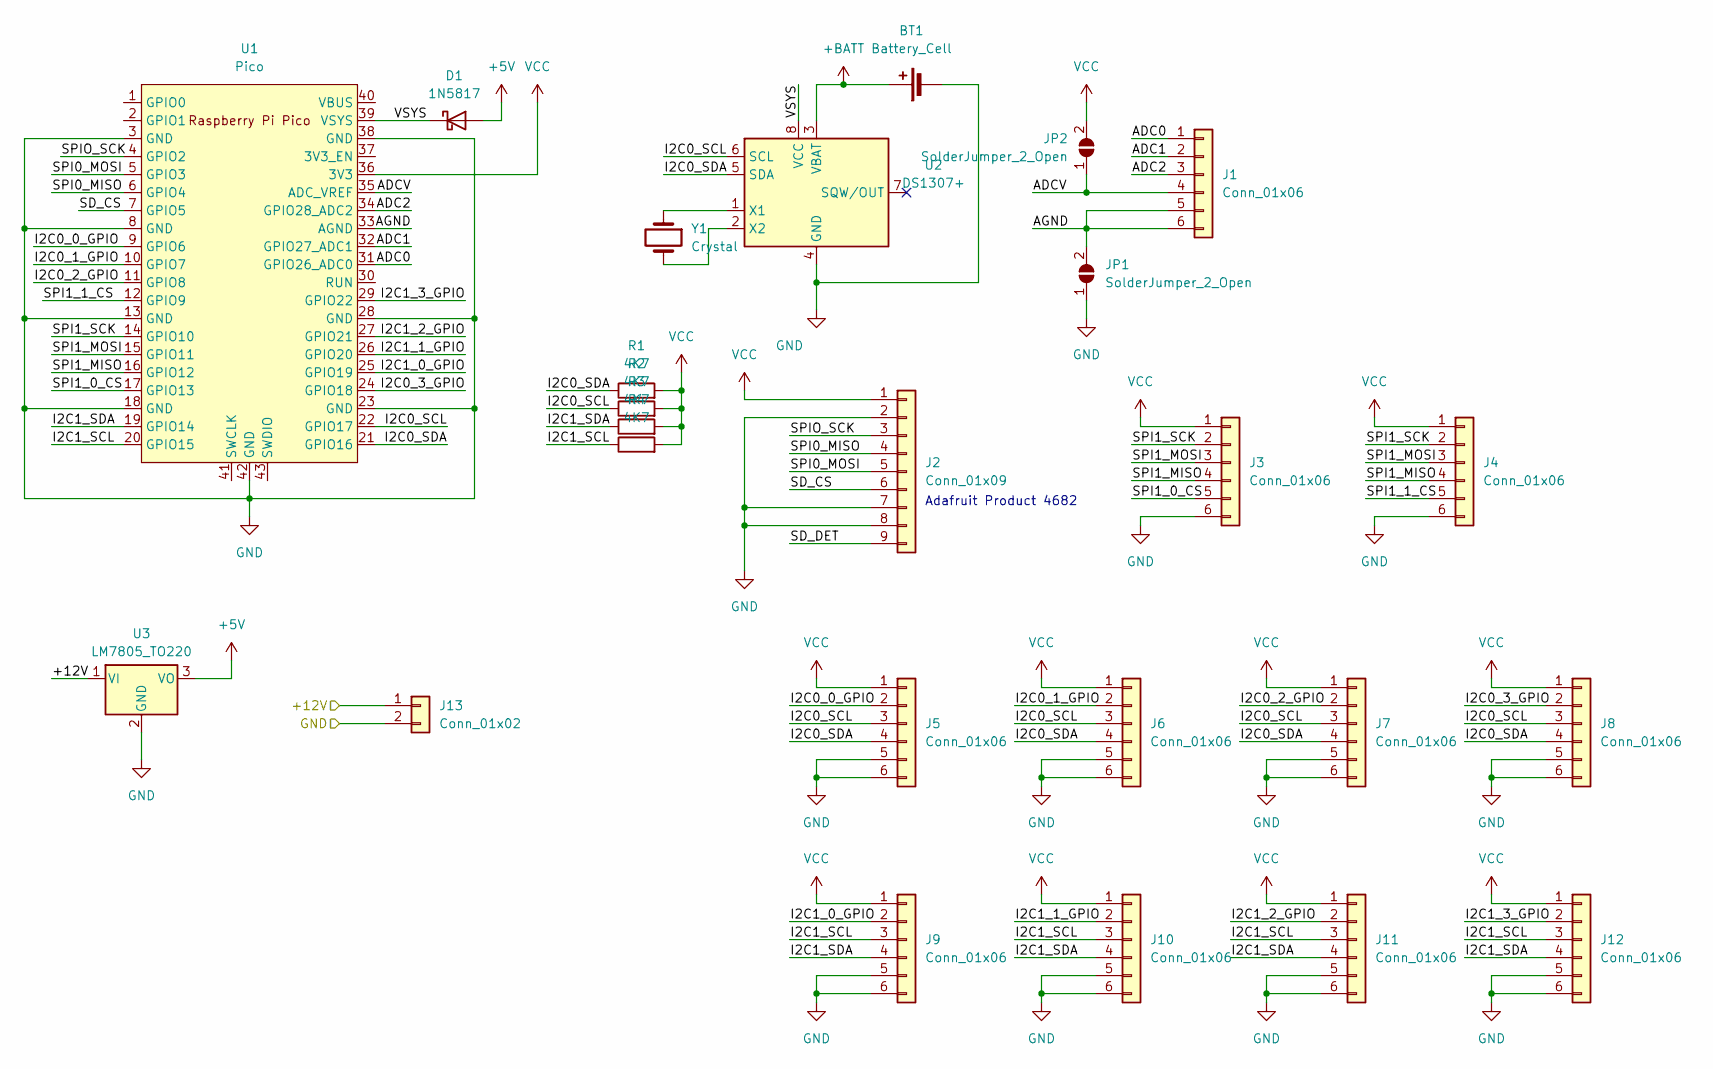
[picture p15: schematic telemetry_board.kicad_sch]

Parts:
BT1: Battery_Cell; RSPRO_237-8341
D1: 1N5817; D_DO-41_SOD81_P10.16mm_Horizontal
J1, J3, J4, J5, J6, J7, J8, J9, J10, J11, J12: Conn_01x06; JST_XA_B06B-XASK-1_1x06_P2.50mm_Vertical
J2: Conn_01x09; Adafruit_MicroSD_Breakout_4682
J13: Conn_01x02; TerminalBlock_bornier-2_P5.08mm
JP1, JP2: SolderJumper_2_Open; SolderJumper-2_P1.3mm_Open_Pad1.0x1.5mm
R1, R2, R3, R4: 4K7; R_Axial_DIN0207_L6.3mm_D2.5mm_P10.16mm_Horizontal
U1: Pico; RPi_Pico_W_SMD_TH
U2: DS1307+; DIP-8_W7.62mm
U3: LM7805_TO220; TO-220-3_Horizontal_TabDown
Y1: Crystal; Crystal_Round_D1.0mm_Vertical

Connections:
+5V: D1.2 (A), U3.3 (VO)
+12V: J13.1, U3.1 (VI)
+BATT: BT1.1 (+), U2.3 (VBAT)
ADC0: J1.1, U1.31 (GPIO26_ADC0)
ADC1: J1.2, U1.32 (GPIO27_ADC1)
ADC2: J1.3, U1.34 (GPIO28_ADC2)
ADCV: J1.4, JP2.1 (A), U1.35 (ADC_VREF)
AGND: J1.5, J1.6, JP1.2 (B), U1.33 (AGND)
GND: BT1.2 (-), J2.2, J2.7, J2.8, J3.6, J4.6, J5.5, J5.6, J6.5, J6.6, J7.5, J7.6, J8.5, J8.6, J9.5, J9.6, J10.5, J10.6, J11.5, J11.6, J12.5, J12.6, J13.2, JP1.1 (A), U1.3 (GND), U1.8 (GND), U1.13 (GND), U1.18 (GND), U1.23 (GND), U1.28 (GND), U1.38 (GND), U1.42 (GND), U2.4 (GND), U3.2 (GND)
I2C0_0_GPIO: J5.2, U1.9 (GPIO6)
I2C0_1_GPIO: J6.2, U1.10 (GPIO7)
I2C0_2_GPIO: J7.2, U1.11 (GPIO8)
I2C0_3_GPIO: J8.2, U1.24 (GPIO18)
I2C0_SCL: J5.3, J6.3, J7.3, J8.3, R2.1, U1.22 (GPIO17), U2.6 (SCL)
I2C0_SDA: J5.4, J6.4, J7.4, J8.4, R1.1, U1.21 (GPIO16), U2.5 (SDA)
I2C1_0_GPIO: J9.2, U1.25 (GPIO19)
I2C1_1_GPIO: J10.2, U1.26 (GPIO20)
I2C1_2_GPIO: J11.2, U1.27 (GPIO21)
I2C1_3_GPIO: J12.2, U1.29 (GPIO22)
I2C1_SCL: J9.3, J10.3, J11.3, J12.3, R4.1, U1.20 (GPIO15)
I2C1_SDA: J9.4, J10.4, J11.4, J12.4, R3.1, U1.19 (GPIO14)
unnamed: U2.1 (X1), Y1.1
unnamed: U2.2 (X2), Y1.2
SD_CS: J2.6, U1.7 (GPIO5)
SD_DET: J2.9
SPI0_MISO: J2.4, U1.6 (GPIO4)
SPI0_MOSI: J2.5, U1.5 (GPIO3)
SPI1_0_CS: J3.5, U1.17 (GPIO13)
SPI1_1_CS: J4.5, U1.12 (GPIO9)
SPI1_MISO: J3.4, J4.4, U1.16 (GPIO12)
SPI1_MOSI: J3.3, J4.3, U1.15 (GPIO11)
SPI1_SCK: J3.2, J4.2, U1.14 (GPIO10)
SPIO_SCK: J2.3, U1.4 (GPIO2)
VCC: J2.1, J3.1, J4.1, J5.1, J6.1, J7.1, J8.1, J9.1, J10.1, J11.1, J12.1, JP2.2 (B), R1.2, R2.2, R3.2, R4.2, U1.36 (3V3)
VSYS: D1.1 (K), U1.39 (VSYS), U2.8 (VCC)

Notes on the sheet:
Adafruit Product 4682

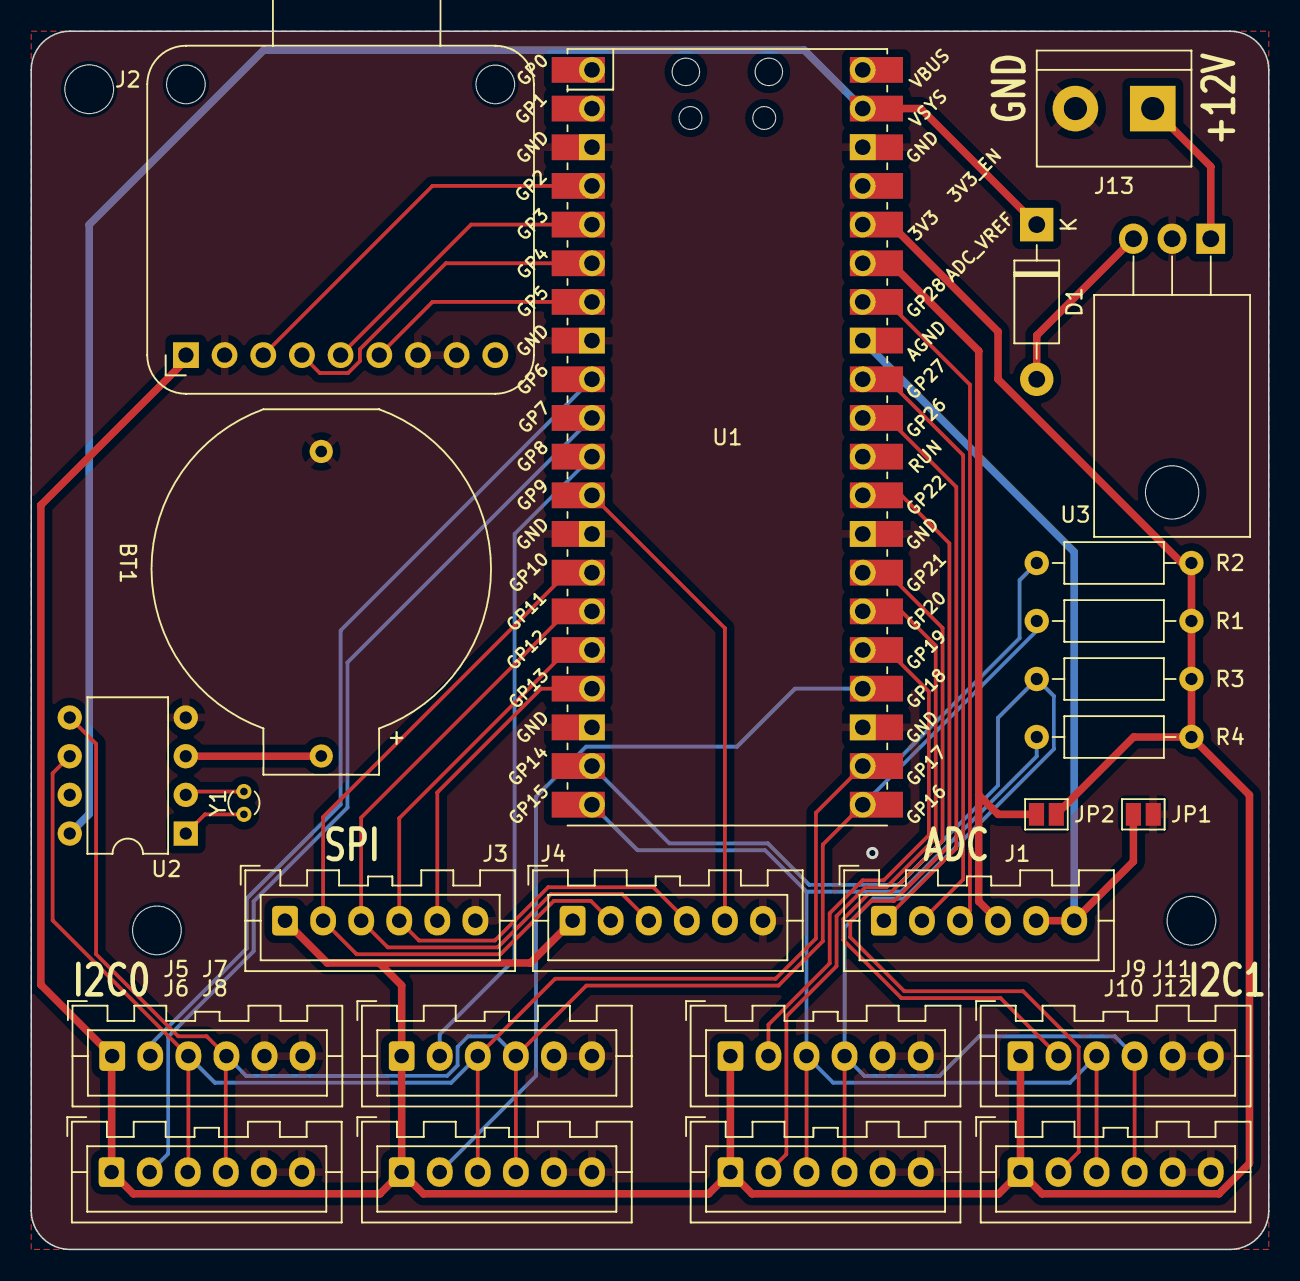
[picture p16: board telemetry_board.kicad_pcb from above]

Board: 2 copper layers, 81.3 x 80.0 mm, 25 parts (0 on the bottom side), 34 nets.

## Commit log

2023-10-15 Reorganized Loom folder
    [BPS.kicad_sch, BSPD.kicad_sch, CAN.kicad_sch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]
2023-10-15 Add start of new BSPD Design
    Currently just includes sensor inputs and the output, and not any
    of the actual logic.
    [New BSPD.kicad_pcb, New BSPD.kicad_sch, trig_plugdet.kicad_sch]
2023-10-15 Add Labels to BPS/TPS Pins
    [New BSPD.kicad_sch]
2023-10-19 Complete most of BSPD State Machine
    TODO: Complete reset signal logic for state machine, to ensure
    we don't power in into a metastable or invalid state.
    [New BSPD.kicad_sch, Timers.kicad_sch, state_machine.kicad_sch]
2023-10-22 Add KiCad caches to gitignore
2023-10-22 Fix BSPD Timing
    [New BSPD.kicad_sch, Timers.kicad_sch, state_machine.kicad_sch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]
2023-10-22 added initial schemaic for can pcb
    [CAN_PCB.kicad_pcb, CAN_PCB.kicad_sch]
2023-10-22 Created relay LED schematic
    [relaybox_indicator_leds.kicad_pcb, relaybox_indicator_leds.kicad_sch]
2023-10-23 Complete BSPD Schematic
    [New BSPD.kicad_sch, Timers.kicad_sch, power.kicad_sch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]
2023-10-23 Schematic designed
    [relaybox_indicator_leds.kicad_pcb, relaybox_indicator_leds.kicad_sch]
2023-10-23 Added footprints and fixed component numbering
    [relaybox_indicator_leds.kicad_pcb, relaybox_indicator_leds.kicad_sch]
2023-10-24 PCB design
    [relaybox_indicator_leds.kicad_pcb, relaybox_indicator_leds.kicad_sch]
2023-10-29 Added the addional inputs to the schematic
    [CAN_PCB.kicad_sch]
2023-10-29 Removed islands and added rounded corners
    [relaybox_indicator_leds.kicad_pcb]
2023-10-29 Complete Schematic, Footprint Assignment, Start PCB Design
    [New BSPD.kicad_pcb, New BSPD.kicad_sch, Timers.kicad_sch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]
2023-10-29 Add BOM
    [New BSPD BOM.xlsx, New BSPD.csv]
2023-10-30 CAN PCB initial layout and schematic changes
    [1729128.psm, 1729128.stp, 9B-16.000MAAJ-B.stp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]
2023-10-30 Fix bug in state machine counters
    Realised that the reset counter would count even in an error
    condition, meaning that if 10 seconds pass after shutdown, it will
    turn back on instantly after the system is ok.
    Fixed by making the reset counter only count if system_ok is high
    [New BSPD.kicad_pcb, state_machine.kicad_sch]
2023-10-30 Add State, Shutdown LEDs, Complete rough board layout
    [New BSPD.kicad_pcb, New BSPD.kicad_sch, state_machine.kicad_sch]
2023-10-31 Add .9in FBR Logo Footprint
2023-10-31 Complete New BSPD!
    TODO: Decide if the crystal needs a capacitor or not
    [New BSPD.kicad_pcb, state_machine.kicad_sch]
2023-11-01 Complete Silkscreen, Fix DRC errors, Misc Cleanup
    [New BSPD.kicad_pcb]
2023-11-03 Add filtering capacitor for crystal power
    [New BSPD.kicad_pcb, New BSPD.kicad_sch]
2023-11-04 Add mounting holes
    [New BSPD.kicad_pcb]
2023-11-12 Complete TelemetryCANBoard schematic
    [TelemetryCANBoard.kicad_pcb, TelemetryCANBoard.kicad_sch]
2023-11-12 Add test points
    [New BSPD.kicad_pcb, New BSPD.kicad_sch, state_machine.kicad_sch]
2023-11-12 Fix BSPD Test Points
    [New BSPD.kicad_pcb]
2023-11-12 Add TelemetryCANBoard BOM
    [TelemetryCANBoard.csv, TelemetryCANBoard.xlsx]
2023-11-12 Add NewBSPD BOM
    [New BSPD.csv, New BSPD.xlsx]
2023-11-13 Made changes to can pcb layout
    [B-06-R-25.step, CAN_PCB.kicad_pcb, CAN_PCB.kicad_sch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]
2023-11-13 Complete TelemetryCANBoard
    [TelemetryCANBoard.kicad_pcb, TelemetryCANBoard.kicad_sch]
2023-11-14 Fix CAN connector
    [TelemetryCANBoard.kicad_pcb]
2023-11-17 Minor layout and silkscreen changes
    [TelemetryCANBoard.kicad_pcb]
2023-11-26 Generated gerbers
    [relaybox_indicator_leds-B_Cu.gbr, relaybox_indicator_leds-B_Mask.gbr, relaybox_indicator_leds-B_Paste.gbr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]
2023-11-29 Add ATF13-2P to BSPD Footprints
2023-11-29 Change BSPD Power connector
    [New BSPD.kicad_pcb, power.kicad_sch]
2024-01-02 Minor changes to pass DRC
    [New BSPD.kicad_pcb]
2024-05-12 Added relaybox indicators to main loom diagram
    [Loom23_detailed.kicad_sch, relaybox_indicator_leds.kicad_sch]
2024-05-12 Add gerbers
    [TelemetryCANBoard-B_Cu.gbl, TelemetryCANBoard-B_Mask.gbs, TelemetryCANBoard-B_Paste.gbp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]
2024-05-15 Changes to the injector numbering
    [Loom23_detailed.kicad_sch, ignition.kicad_sch, relaybox_indicator_leds.kicad_sch]
2024-05-18 Fixed injector high side labels
    [Loom23_detailed.kicad_sch]
2024-05-19 Added the neutral and shutdown LEDs to dash
    [Loom23_detailed.kicad_sch, dash_switches.kicad_sch]

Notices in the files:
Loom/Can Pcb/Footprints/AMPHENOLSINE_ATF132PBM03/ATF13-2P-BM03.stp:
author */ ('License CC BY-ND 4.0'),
